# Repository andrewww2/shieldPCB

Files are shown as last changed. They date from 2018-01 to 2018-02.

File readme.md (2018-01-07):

Arduino shield for CaBot
=============================
The motor driver is copied from the Solarbotics L298 driver: https://solarbotics.com/product/k_cmd/

Parts list: see Team G order sheet for parts requested on 1/3/18

Questions and comments for team/Navarro:
1) Should we connect the motor driver LDO 5V with the Arduino's 5V? 
	I think this means the Arduino will be powered from 12V (Arduino turned on whenever CaBot is powered on)
2) Will EMI from motor driver cause problems with the sensors?
	We can connect capacitors across motor terminals to reduce EMI
3) We need to protect against static shock. See included document: "ESD considerations for touch sensing...": 
	i) Connect resistor in series with touch pad
	ii) Using Kapton tape to cover touch pad

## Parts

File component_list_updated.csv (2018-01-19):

Qty | Value | Device | Package | Parts | Description
3 | 0.1 uF | C-US025-050X050 | C025-050X050 | C2, C3, C4 | CAPACITOR, American symbol
2 | 1.8K | R-US_0207/10 | 0207/10 | R3, R4 | RESISTOR, American symbol
4 | 1K | R-US_0207/10 | 0207/10 | R5, R6, R7, R8 | RESISTOR, American symbol
8 | 1N4004 | 1N4004 | DO41-10 | D1, D2, D3, D4, D5, D6, D7, D8 | DIODE
1 | 1X2-3.5MM | 1X2-3.5MM | 1X2-3.5MM | 12V_IN | 3.5mm Terminal block
1 | 22 uF | CPOL-USB45181A | B45181A | C1 | POLARIZED CAPACITOR, American symbol
1 | 330 | R-US_0207/10 | 0207/10 | R9 | RESISTOR, American symbol
2 | 47K | R-US_0207/10 | 0207/10 | R1, R2 | RESISTOR, American symbol
1 | ADA_MPR121 | ADA_MPR121 | ADA_MPR121 | U$1
1 | BNO055 | BNO055 | BNO055 | IMU1
1 | E-SWITCH_500SSP1S2M2QEA | E-SWITCH_500SSP1S2M2QEA | E-SWITCH_500SSP1S2M2QEA | U$2
2 | GREEN | LED3MM | LED3MM | LED1, LED3 | LED
1 | L298 | L298 | MULTIWATT-15 | IC1 | DUAL FULL-BRIDGE DRIVER
1 | LM2937ET-5V | LM2937ET-5,0 | TO220(V) | IC2 | 400 and 500 mA Low Dropout Voltage Regulator
1 | MOTOR1_HEADER | PINHD-1X6 | 1X06 | JP1 | PIN HEADER
1 | MOTOR2_HEADER | PINHD-1X6 | 1X06 | JP2 | PIN HEADER
1 | Mega R3 | ARDUINO-MEGAFULL | ARDUINO_MEGA | J2 | Arduino MegaR3 board footprint. Also works for Due.
2 | RED | LED3MM | LED3MM | LED2, LED4 | LED
1 | Reset | 10-XX | B3F-10XX | S2 | OMRON SWITCH
1 | STATUS | LED3MM | LED3MM | LED5 | LED

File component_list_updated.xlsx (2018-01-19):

Qty | Value | Device | Package | Parts | Description | Do we have it?
8 | 1N4004 | 1N4004 | DO41-10 | D1, D2, D3, D4, D5, D6, D7, D8 | DIODE
4 | 1K | R-US_0207/10 | 0207/10 | R5, R6, R7, R8 | RESISTOR, American symbol
3 | 0.1 uF | C-US025-050X050 | C025-050X050 | C2, C3, C4 | CAPACITOR, American symbol
2 | 2.2K | R-US_0207/10 | 0207/10 | R3, R4 | RESISTOR, American symbol
2 | 47K | R-US_0207/10 | 0207/10 | R1, R2 | RESISTOR, American symbol
2 | GREEN | LED3MM | LED3MM | LED1, LED3 | LED
2 | RED | LED3MM | LED3MM | LED2, LED4 | LED
1 | 1X2-3.5MM | 1X2-3.5MM | 1X2-3.5MM | 12V_IN | 3.5mm Terminal block
1 | 22 uF | CPOL-USB45181A | B45181A | C1 | POLARIZED CAPACITOR, American symbol
1 | 390 | R-US_0207/10 | 0207/10 | R9 | RESISTOR, American symbol
1 | ADA_MPR121 | ADA_MPR121 | ADA_MPR121 | U$1
1 | BNO055 | BNO055 | BNO055 | IMU1
1 | E-SWITCH_500SSP1S2M2QEA | E-SWITCH_500SSP1S2M2QEA | E-SWITCH_500SSP1S2M2QEA | U$2
1 | L298 | L298 | MULTIWATT-15 | IC1 | DUAL FULL-BRIDGE DRIVER
1 | LM2937ET-5V | LM2937ET-5,0 | TO220(V) | IC2 | 400 and 500 mA Low Dropout Voltage Regulator
1 | MOTOR1_HEADER | PINHD-1X6 | 1X06 | JP1 | PIN HEADER
1 | MOTOR2_HEADER | PINHD-1X6 | 1X06 | JP2 | PIN HEADER
1 | Mega R3 | ARDUINO-MEGAFULL | ARDUINO_MEGA | J2 | Arduino MegaR3 board footprint. Also works for Due.
1 | Reset | 10-XX | B3F-10XX | S2 | OMRON SWITCH
1 | STATUS | LED3MM | LED3MM | LED5 | LED
x | Female headers |  |  |  |  | Where did Chris get them?

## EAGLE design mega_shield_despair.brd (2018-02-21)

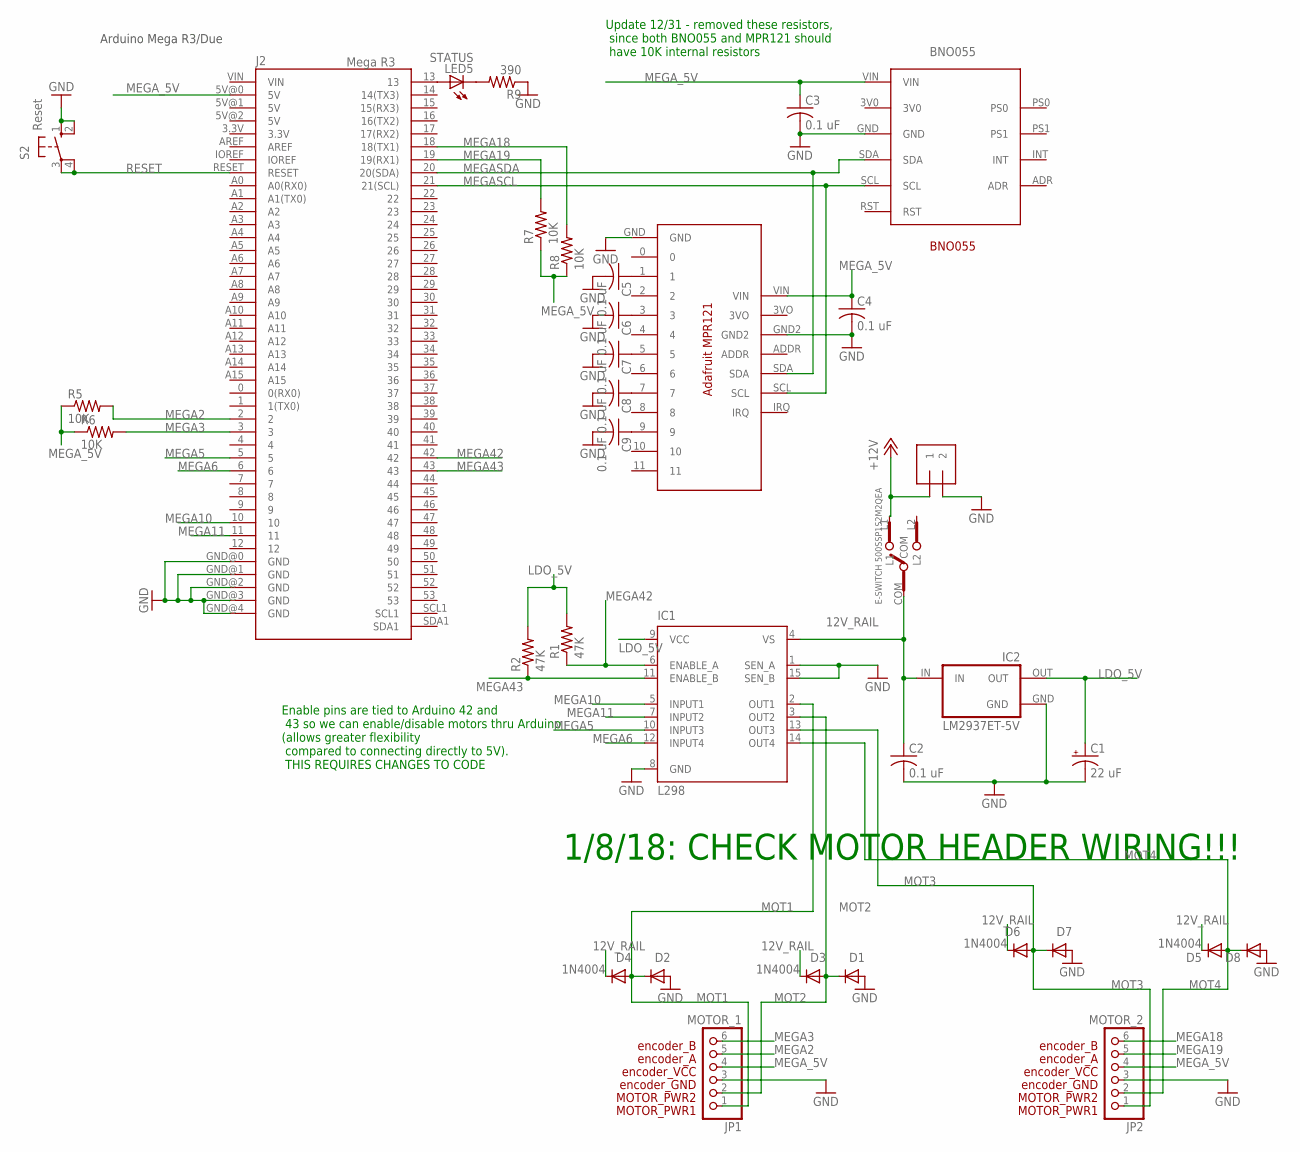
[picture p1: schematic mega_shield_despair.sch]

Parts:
12V_IN: 1X2-3.5MM
BNO055: BNO055
C1: 22 uF; B45181A
C2, C3, C4, C5, C6, C7, C8, C9: 0.1 uF; C025-050X050
D1, D2, D3, D4, D5, D6, D7, D8: 1N4004; DO41-10
IC1: L298; MULTIWATT-15
IC2: LM2937ET-5V; TO220(V)
J2: Mega R3; ARDUINO_MEGA
JP1: MOTOR_1; 1X06
JP2: MOTOR_2; 1X06
LED5: STATUS; LED3MM
MPR121: ADA_MPR121
R1, R2: 47K; 0207/10
R5, R6, R7, R8: 10K; 0207/10
R9: 390; 0207/10
S2: Reset; B3F-10XX
SLIDE_SW: E-SWITCH_500SSP1S2M2QEA

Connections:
12V_RAIL: C2.1, D3.C, D4.C, D5.C, D6.C, IC1.4 (VS), IC2.IN, SLIDE_SW.COM
+12V: 12V_IN.1, SLIDE_SW.L1
GND: 12V_IN.2, BNO055.GND, C1.-, C2.2, C3.2, C4.2, C5.2, C6.2, C7.2, C8.2, C9.2, D1.A, D2.A, D7.A, D8.A, IC1.1 (SEN_A), IC1.8 (GND), IC1.15 (SEN_B), IC2.GND, J2.GND@0 (GND), J2.GND@1 (GND), J2.GND@2 (GND), J2.GND@3 (GND), J2.GND@4 (GND), JP1.3, JP2.3, MPR121.GND, MPR121.GND2, R9.1, S2.1 (S), S2.2 (S1)
LDO_5V: C1.+, IC1.9 (VCC), IC2.OUT, R1.2, R2.2
MEGA2: J2.2, JP1.5, R5.2
MEGA3: J2.3, JP1.6, R6.2
MEGA5: IC1.10 (INPUT3), J2.5
MEGA6: IC1.12 (INPUT4), J2.6
MEGA10: IC1.5 (INPUT1), J2.10
MEGA11: IC1.7 (INPUT2), J2.11
MEGA18: J2.18 (18(TX1)), JP2.6, R8.2
MEGA19: J2.19 (19(RX1)), JP2.5, R7.2
MEGA42: IC1.6 (ENABLE_A), J2.42, R1.1
MEGA43: IC1.11 (ENABLE_B), J2.43, R2.1
MEGASCL: BNO055.SCL, J2.21 (21(SCL)), MPR121.SCL
MEGASDA: BNO055.SDA, J2.20 (20(SDA)), MPR121.SDA
MEGA_5V: BNO055.VIN, C3.1, C4.1, J2.5V@0 (5V), JP1.4, JP2.4, MPR121.VIN, R5.1, R6.1, R7.1, R8.1
MOT1: D2.C, D4.A, IC1.2 (OUT1), JP1.1
MOT2: D1.C, D3.A, IC1.3 (OUT2), JP1.2
MOT3: D6.A, D7.C, IC1.13 (OUT3), JP2.1
MOT4: D5.A, D8.C, IC1.14 (OUT4), JP2.2
unnamed: C5.1, MPR121.1
unnamed: C6.1, MPR121.3
unnamed: J2.13, LED5.A
unnamed: LED5.K (C), R9.2
unnamed: C7.1, MPR121.5
unnamed: C8.1, MPR121.7
unnamed: C9.1, MPR121.9
RESET: J2.RESET, S2.3, S2.4 (P1)

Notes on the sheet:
Arduino Mega R3/Due
Update 12/31 - removed these resistors, since both BNO055 and MPR121 should have 10K internal resistors
Enable pins are tied to Arduino 42 and 43 so we can enable/disable motors thru Arduino (allows greater flexibility compared to connecting directly to 5V). THIS REQUIRES CHANGES TO CODE
1/8/18: CHECK MOTOR HEADER WIRING!!!

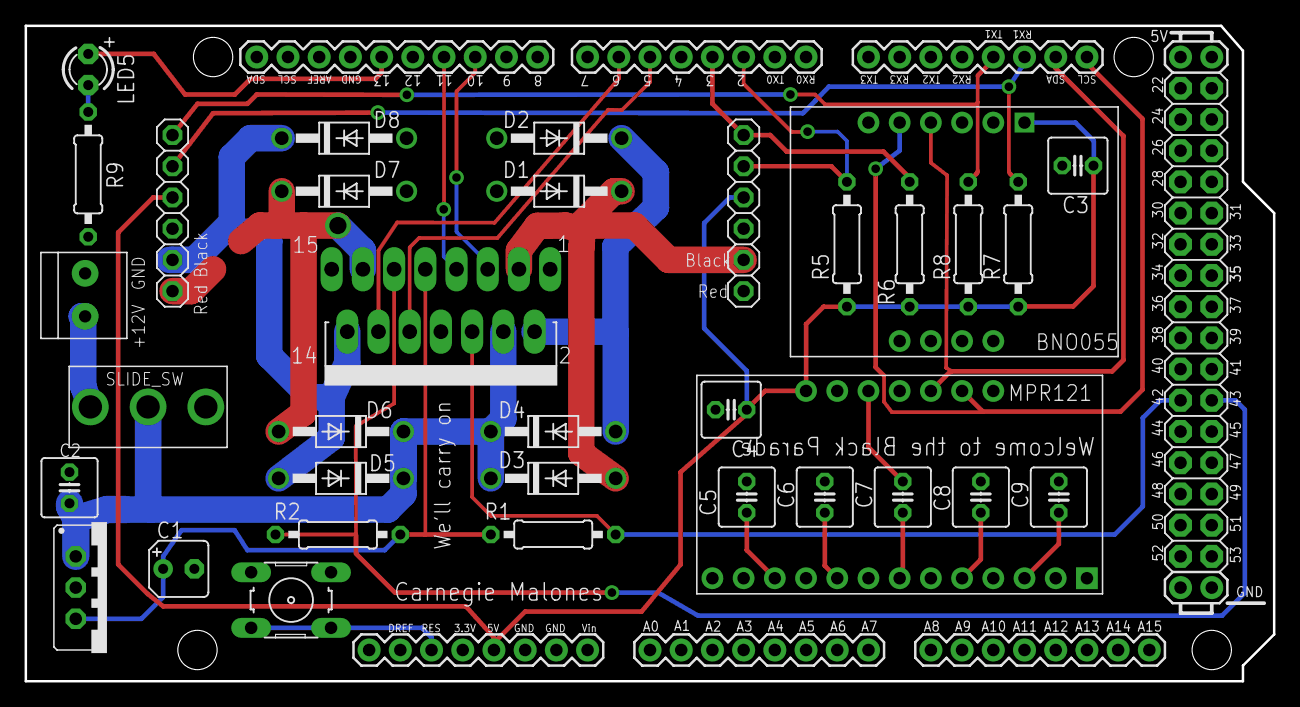
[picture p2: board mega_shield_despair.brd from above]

Board: 2 copper layers, 101.6 x 53.3 mm, 35 parts (0 on the bottom side), 29 nets.

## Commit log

2018-01-07 Init commit
    [mega_shield2.brd, mega_shield2.sch]
2018-01-07 Minor changs to component placement
    [mega_shield2.brd]
2018-01-08 Added 6 pin motor headers
    [mega_shield2.brd, mega_shield2.sch]
2018-01-17 Added restricts to ground plane in brd file
    [mega_shield2.brd, mega_shield2.sch]
2018-01-17 Added switch to library, shifted components around on brd
    [mega_shield2.brd, mega_shield2.sch]
2018-01-19 added excel component list, changed resistor values
    [component_list_updated.csv, component_list_updated.xlsx, mega_shield2.brd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]
2018-01-24 changes to silkscreen
    [mega_shield2.brd, mega_shield2.sch]
2018-01-25 shifted some components around, edited silkscreen
    [mega_shield2.brd, mega_shield2.sch]
2018-01-26 final gerber files
    [mega_shield3.GBL, mega_shield3.GBO, mega_shield3.GBP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]
2018-02-21 add despair version
    [mega_shield_despair.brd, mega_shield_despair.sch]
